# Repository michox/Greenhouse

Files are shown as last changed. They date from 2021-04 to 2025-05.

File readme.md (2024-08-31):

# Greenhouse

My mother grows her own food as a hobby and is very passionate about it. I usually benefit a lot from this hobby since as a vegetarian I get basically all my food from my mother&#39;s garden during the summer months. On top of that, organic home-grown food is not only much richer in nutrients and free of pesticides, it also tastes a lot better in my experience. Since I will be moving out and will no longer be able to help water the plants, I decided to use my engineering skills to build her an automated gardening system which takes care of her greenhouse and the three 5 m² raised bed fields.

# User Requirements

After talking to my mother about her needs with the system, I came up with the following user requirements.

| **ID** | **Description** |
| --- | --- |
| UREQ-001 | Must deliver water to 4 separate fields with an average of 20L per day on a dry, sunny day and 0-5L on a cloudy or rainy day |
| UREQ-002 | Could keep the soil at a configured moisture level between 0-100% |
| UREQ-003 | Must ventilate when the temperature in the green house reaches a user set temperature |
| UREQ-004 | Must heat actively when the temperature in the green house drops below a user set temperature |
| UREQ-005 | Should fend of snails effectively |
| UREQ-006 | Should not kill snails so as not to attract more snails |
| UREQ-007 | Must Monitor minimum and maximum temperatures over the day |
| UREQ-008 | Must be powered by solar since no grid connection is available in the garden |
| UREQ-009 | Must be low-cost |
| UREQ-010 | Must operate during 3 cloudy summer days in a row |
| UREQ-011 | Monitor must be easily readable from 50cm |
| UREQ-012 | Must be repairable |
| UREQ-013 | Must be safe |
| UREQ-014 | Must not break down in the first year |
| UREQ-015 | Should be low noise |

# System Diagram

The first thing I usually do is to define the different functional elements of a system together with inputs and outputs. I like to do that in a system diagram because it is intuitive and easy to read. I could use standardized symbols, but since I want this project to be accessible to hobbyists, I&#39;ll keep it simple and visual.

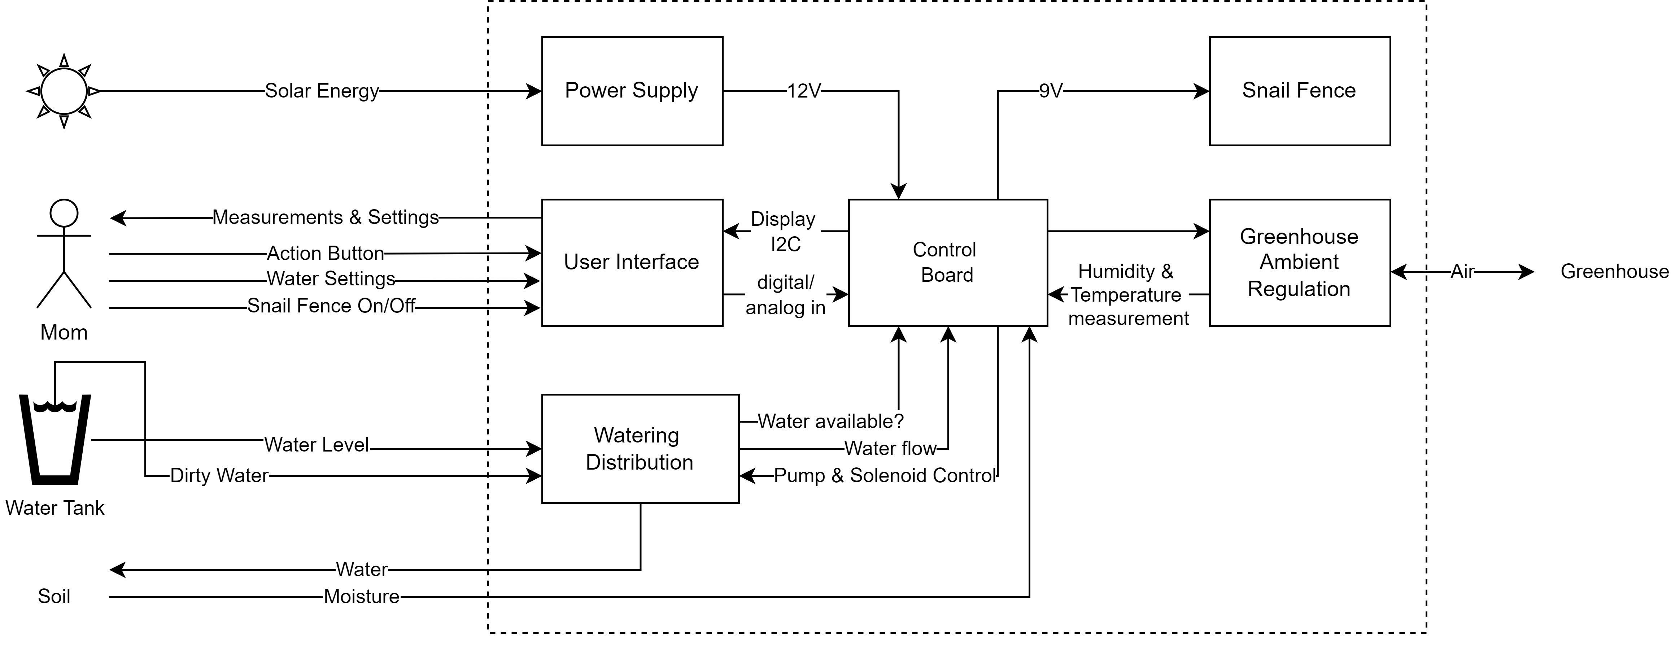
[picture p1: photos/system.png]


# System Requirements

Next, I thought about what parts my system would need to consist of and what each of these parts must fulfill to cover the user requirements. I did not take this too seriously and did not go into all the detailed module requirements like the behavior requirements of the software. This was just to document my thinking process and practice my product requirements skills a little.

| **ID** | **Description** | **Trace** |
| --- | --- | --- |
| | **Wiring** | |
| REQ-001 | All cables need to be detachable with little effort for maintenance purposes | > UREQ-011 |
| REQ-002 | All wires must exceed the standard diameters based on the rated amperage of the attached utility | > UREQ-013 |
| | **Water Distribution** | |
| REQ-011 | Must have a pump that delivers a set amount of water up to 40 Liter per day to four different locations based on user input | > UREQ-001 |
| REQ-012 | Could deliver separate amounts of water up to 40 Liter per day to four different locations based on moisture readings | > UREQ-002 |
| REQ-013 | Could have hygrometers in each field | > REQ-012 |
| REQ-014 | Must have a flowmeter with a measuring range compatible to the selected pump | > REQ-011 |
| REQ-015 | Must take the water from a water tank with potentially dirty water | > UREQ-001 |
| REQ-016 | Pump must not run dry | > UREQ-014 |
| | **User Interface** | |
| REQ-021 | Display must be at least 1.3&quot; | > UREQ-010 |
| REQ-022 | Must have a means to set the water/humidity for each field | > UREQ-001 |
| REQ-023 | Must have a means to configure the internal clock | > UREQ-001 |
| REQ-024 | Must display the minimum and maximum temperature and humidity over the day | > UREQ-007 |
| REQ-025 | Must allow to set a minimum temperature at which heating is turned on | > UREQ-004 |
| REQ-026 | Must allow to set a maximum temperature at which ventilation is turned on | > UREQ-003 |
| | **Control Board** | |
| REQ-031 | Must be protected from rain and/or condensation | > UREQ-014 |
| | **Snail Fence** | |
| REQ-041 | Must surround each of the three 1m x 5m raised beds with two copper tapes attached to a 9V power supply | > UREQ-005 > UREQ-006 |
| REQ-042 | should have a switch to turn off | > UREQ-006 |
| | **Greenhouse Ambient Regulation** | |
| REQ-051 | Must have a 12V fan | > REQ-061 > UREQ-003 |
| REQ-052 | Must have a 12V heater | > REQ-061 > UREQ-004 |
| REQ-053 | Must have a temperature and humidity sensor | > UREQ-004 |
| | **Power Supply** | |
| REQ-061 | Must have a battery with twice the capacity to power the controller module and operate the pump long enough to deliver a total of 80L per day for three days in a row. | > UREQ-001 > UREQ-008 |
| REQ-062 | Battery must be a 12V lead acid battery for cost effectiveness (because we had an old one laying around) | > UREQ-009 |
| REQ-063 | Must have a solar panel that generates enough electricity to charge the battery on an average sunny day in germany through a charge controller as constrained by> REQ-061 | > UREQ-010 > UREQ-008 |
| REQ-064 | Must provide enough power for the fan | > UREQ-003 |
| REQ-065 | Must provide enough power for the heater | > UREQ-004 |
| REQ-066 | Must provide enough power for the water distribution system | > UREQ-001 |
| REQ-067 | Must provide enough power for the snail fence | > UREQ-005 |

# System Design

Next, I started looking for parts and thinking about how I may build it cost-effectively with the parts on the market. There is no point in designing the perfect system if you can&#39;t build it because you can&#39;t find the right parts. For example, I had to get multiple adapters between thread sizes and a pressure regulator because the pump would deliver more pressure than the drip hose could endure. I made a more detailed module diagram of the water distribution since this one was the most complicated and I wanted to visualize what adaptors I needed and how everything fits together.

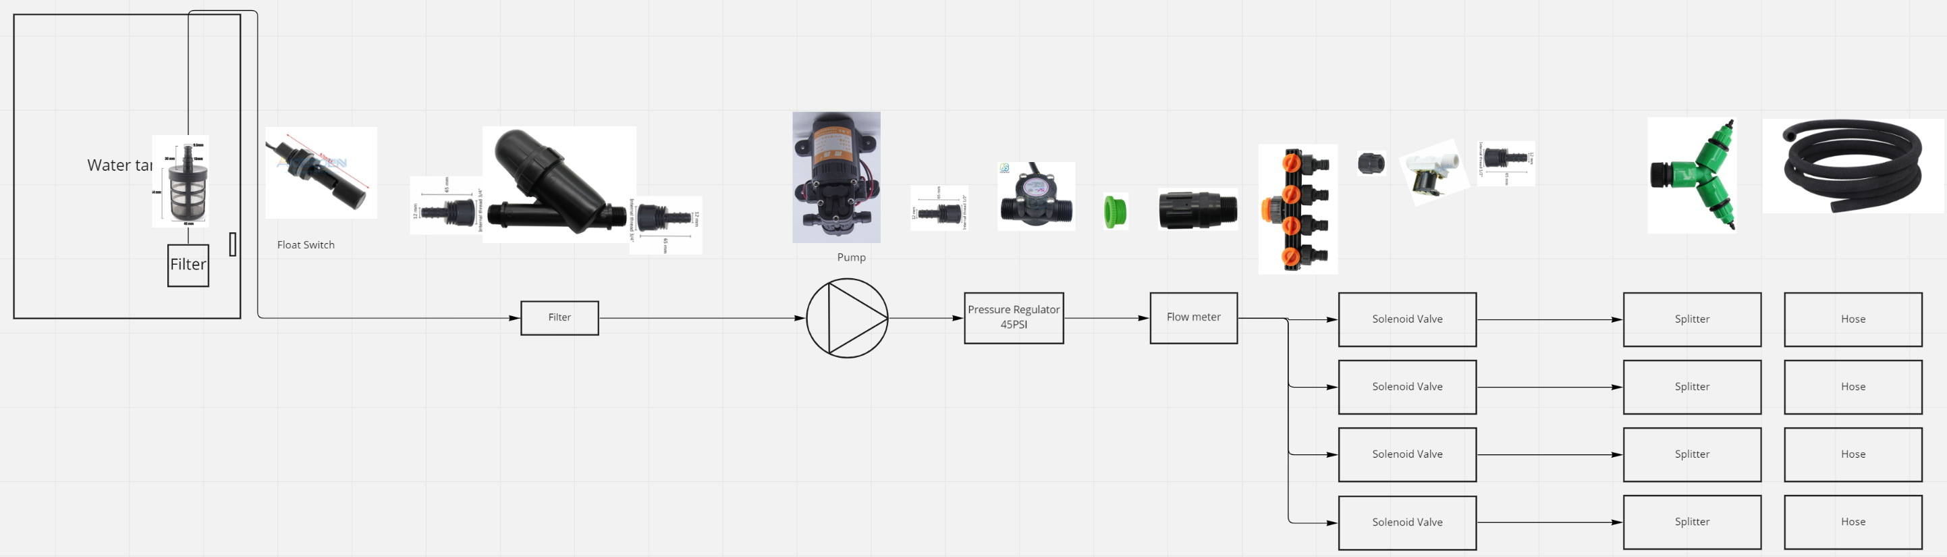
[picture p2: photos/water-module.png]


I thought about making diagrams for the electronics and software as well. but I feel like the code and electronic schematics are pretty self-explanatory, and since I am a busy man, I will leave it at that. If you have any questions, please create a github issue and I will try to answer it.

# Parts

Since my mother did not want me to spend much money, I ordered most parts from AliExpress which arrived within 2-4 weeks. Since I did not write down all requirements, traceability kind of loses its purpose so I&#39;ll leave it out.

| **ID** | **Description** | **Properties** | **Requirements** | **Quantity** | **Price €** | **Buy** |
| --- | --- | --- | --- | --- | --- | --- |
| PART-001 | Hose | 20m, 12mm inner diameter | low-cost, tolerate pressure of pump | 1 | 10 | get locally |
| PART-002 | Dripping Hose | 20m length 4/9mm, minimum of 1-2 bar working pressure, maximum of 4 bar | | 4 | 11,43 | [Link](https://www.aliexpress.com/item/32929487096.html) |
| PART-003 | Hose Clamp | 3/4&quot;, 5pc per pack | 3/4&quot; | 2 | 0,86 | [Link](https://www.aliexpress.com/item/4000954734119.html) |
| PART-004 | Pump | 5 Bar, 3.5 L/min | Flow Rate, Pressure | 1 | 8,46 | [Link](https://www.aliexpress.com/item/1005001612894964.html) |
| PART-005 | Flow Meter | 1-30L/min, 17.5 Bar, 1/2&quot; threads | 12V, can handle the pressure | 1 | 1,60 | [Link](https://www.aliexpress.com/item/4000074968315.html) |
| PART-006 | Inlet Filter | Double Net | Easy to clean, hang into water | 1 | 2,64 | [Link](https://www.aliexpress.com/item/33054351075.html) |
| PART-007 | Pre-pump Filter | 3/4&quot; threads | connectors on both ends | 1 | 6,34 | [Link](https://www.aliexpress.com/item/32906764639.html) |
| PART-008 | Pressure Regulator | 3 Bar, 3/4&quot; in female, 3/4&quot; out male, | less than 4 bar PART-002 | 1 | 1,58 | [Link](https://www.aliexpress.com/item/32917089441.html) |
| PART-009 | 1/2&quot; to 3/4&quot; adapter | | low cost UREQ-009 | 4 | 0,45 | [Link](https://www.aliexpress.com/item/4000177787641.html) |
| PART-010 | Adaptor 1/2&quot;to hose | | 1/2&quot; internal thread12mm barbed connector (PART-001) | 5 | 0,43 | [Link](https://www.aliexpress.com/item/32917141441.html) |
| PART-011 | Adaptor 3/4&quot;to hose | | 3/4&quot; internal thread12mm barbed connector (PART-001) | 2 | 0,43 | [Link](https://www.aliexpress.com/item/32917141441.html) |
| PART-012 | Fan | | 12Vlow noise | 2 | 3,27 | [Link](https://www.aliexpress.com/item/4001007637782.html) |
| PART-013 | 4 Way hose splitter | | can screw into solenoid | 1 | 5,51 | [Link](https://www.aliexpress.com/item/32923580377.html) |
| PART-014 | Soaking hose connector | | 4mm outside3/4&quot; splitter | 4 | 1,86 | [Link](https://www.aliexpress.com/item/32936271677.html) |
| PART-015 | Solenoid Valve | 1/2&quot; threads, 0.2-8 bar | runs at 12V, normally closed | 4 | 1,36 | [Link](https://www.aliexpress.com/item/33007085127.html) |
| PART-016 | Float Switch | | mounts to side of the tank | 2 | 0,64 | [Link](https://www.aliexpress.com/item/4001061701102.html) |
| PART-017 | Solar Panel | 20W | >= 4x battery capacity | 1 | 22,17 | [Link](https://www.aliexpress.com/item/32847502994.html) |
| PART-018 | Solar Charge Controller | 10A | for lead acid batteries, | 1 | 3,66 | [Link](https://www.aliexpress.com/item/33007101009.html) |
| PART-019 | Battery | 60Wh | low-cost, >= 60 Wh | 1 | 18 | get locally |
| PART-020 | Heater | | 100W, 12V | 1 | 10,59 | [Link](https://www.aliexpress.com/item/32967951841.html) |
| PART-021 | ESP32 | | low-cost, I2C interface, USB flashing, | 1 | 4,62 | [Link](https://www.aliexpress.com/item/32834130422.html) |
| PART-022 | Real Time Clock module | Based on PCF8563T | I2C, Battery mount | 1 | 0,32 | [Link](https://aliexpress.com/item/1005006438572175.html) |
| PART-023 | Hygrometer | Analog reading | 3.3V, low-cost | 8 | 0,23 | [Link](https://www.aliexpress.com/item/33048567290.html) |
| PART-024 | Bare Copper Wire | 25mx0.9mm | without enameling  | 2 | 12 | [Link](https://www.aliexpress.com/item/4000308076266.html) |
| PART-025 | 5V Step Down Converter | input 6-32V, output 5V 2A, | input 12V, output 1A | 1 | 2,18 | [Link](https://www.aliexpress.com/item/32960561943.html) |
| PART-026 | Micro USB Cable | for code uploading and powering of the USB | 20cm length, capable of data transmission | 1 | 2,18 | get locally |
| PART-027 | Button | Standard Button 12x12mm | 1 | 1 | [Link](https://www.aliexpress.com/item/32912175986.html) |
| PART-028 | I2C Display | 1.3&quot;, OLED | I2C communication | 1 | 3,15 | [Link](https://www.aliexpress.com/item/4001145494936.html) |
| PART-029 | HTU31D Humidity &amp; Temperature Sensor | 0-100% humidity, -40 to +125 C, | 0-100% humidity, -10 to +60 C, resistant to condensation, breakout so it can be lead outside of the enclosure | 1 | 2,57 | [Link](https://www.aliexpress.com/item/1005003128666097.html) |
| PART-030 | Connectors | | 2,3,4 pin connectors, suitable for selected wire diameter | 1 | 1,52 | [Link](https://www.aliexpress.com/item/32836912971.html) |
| PART-031 | Potentiometers | WTH118 linear Potentiometer | fully enclosed, else there are issues with humidity | 4 | 1,30€ | [Link](https://de.aliexpress.com/item/1005003579523720.html) | 
| PART-032 | PCB | See electronics folder for detailed BOM | | 1 | 15 | ordered from JLCPCB using the files in the electronics folder | 
| PART-033 | Barbed Connector adaptor | I 3D printed this from TPU because I realized later that I was missing this part | flexible, convert 9mm outer diameter to 12mm outer diameter | 1 | 0,05 | |

# Electronics
After a first iteration using a prototype through-hole circuit board and several bug-fixes, I upgraded to a PCB for version 2. The schematics and PCB design can be found at 
https://www.flux.ai/michox/greenhouse?editor=schematic

Since the MOQ on JLCPCB was 5 pieces I have a few more PCBs left, so if you are interested in one of those, contact me by raising an issue.

# Future Improvements
Since I regularly upload to the PCB while connected to the main power supply, I decided to use a USB step-down converter rather than an onboard voltage regulator, as I would otherwise have issues with the USB power Supply and the onboard PCB power supply. 

In the future, integrating the power supply for the ESP32 and the RTC Module would be opportunities for improvement. The PCB is also larger than necessary as I wanted to keep my old enclosure, but the PCB could easily be half the size.

I will also consider designing an enclosure for 3D printing.

# Pictures

Me assembling the box.
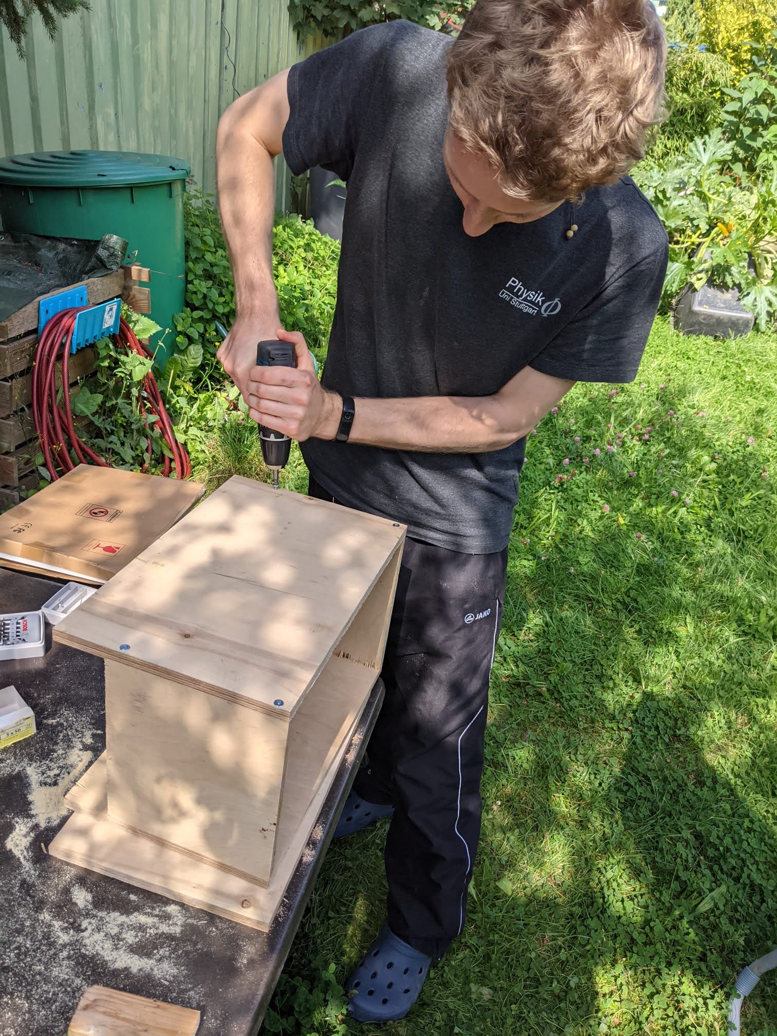
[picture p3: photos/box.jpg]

I did not have any hinges so I 3D printed some with my resin printer
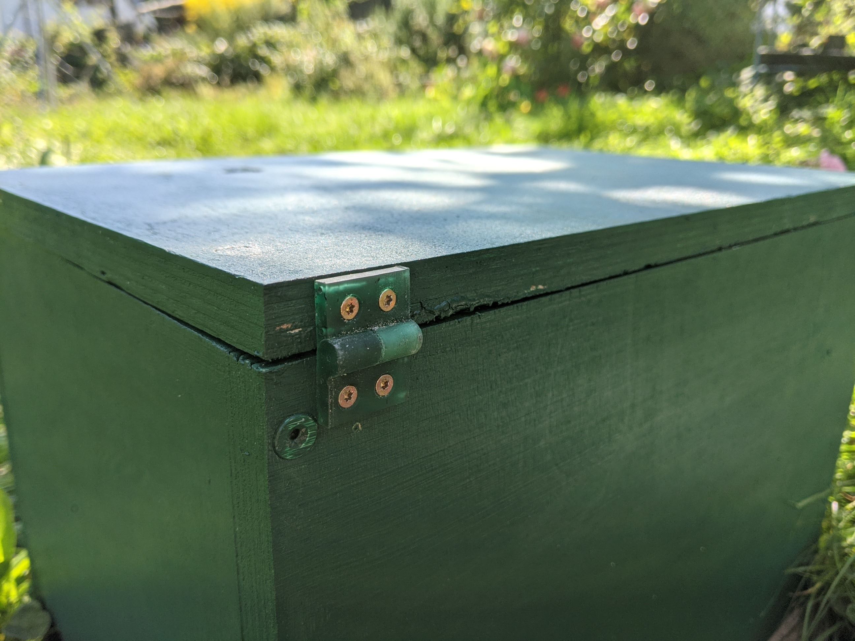
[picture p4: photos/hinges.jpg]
 
They work!
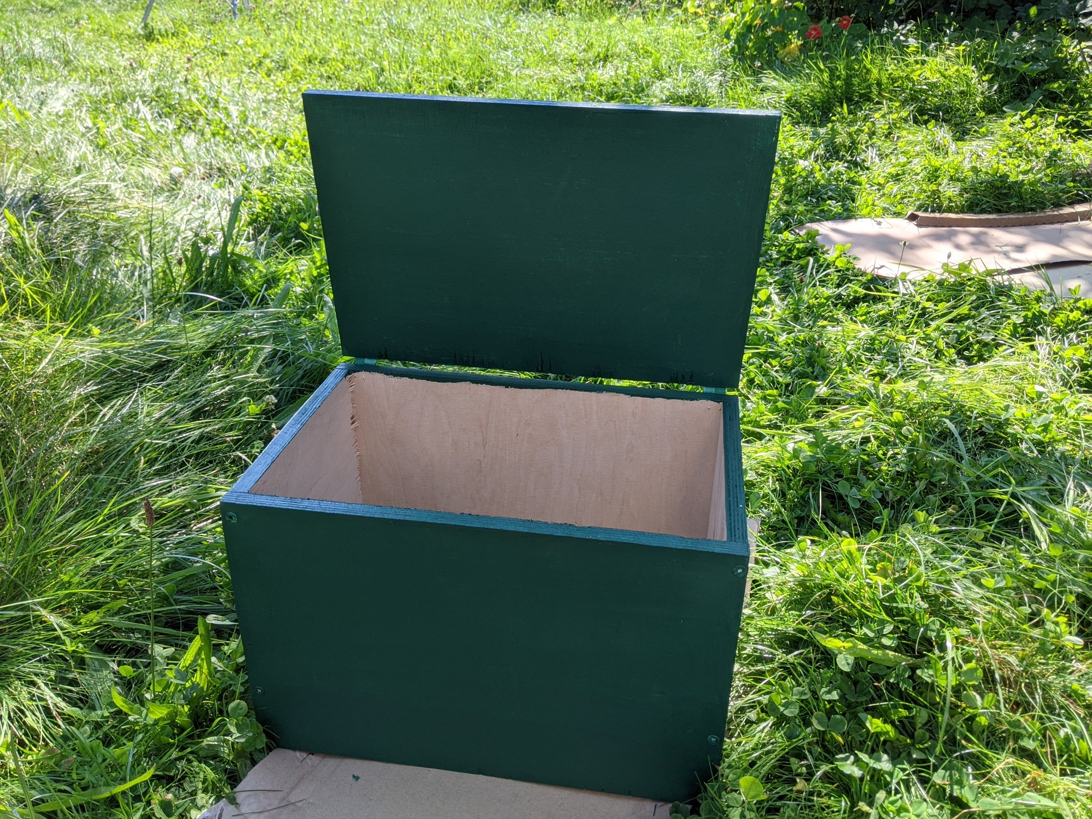
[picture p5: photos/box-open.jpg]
 
Assembling the electronics
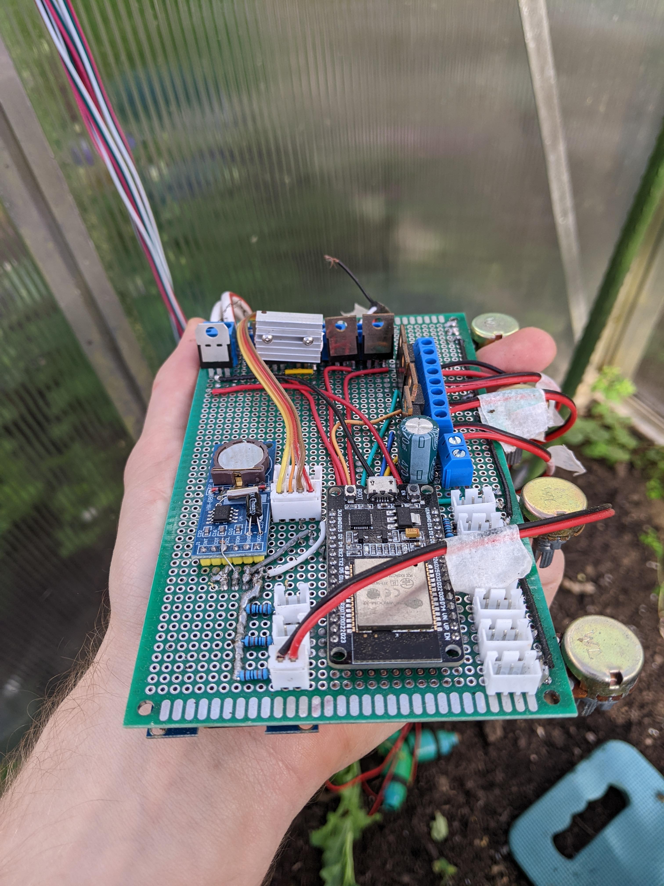
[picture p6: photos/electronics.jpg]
 
the fans
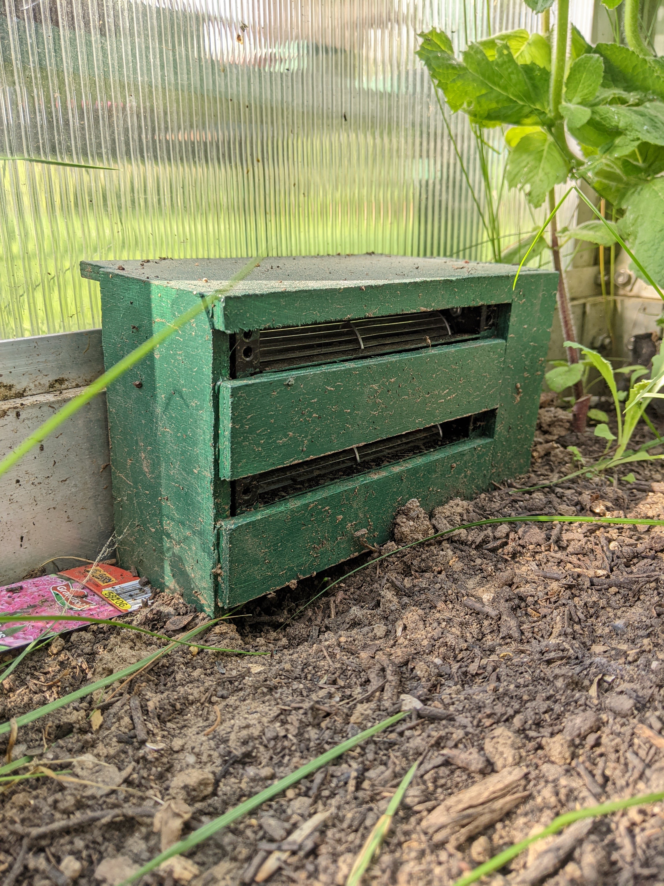
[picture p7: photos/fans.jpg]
 
this is where the fans get their air from
 
solar panel
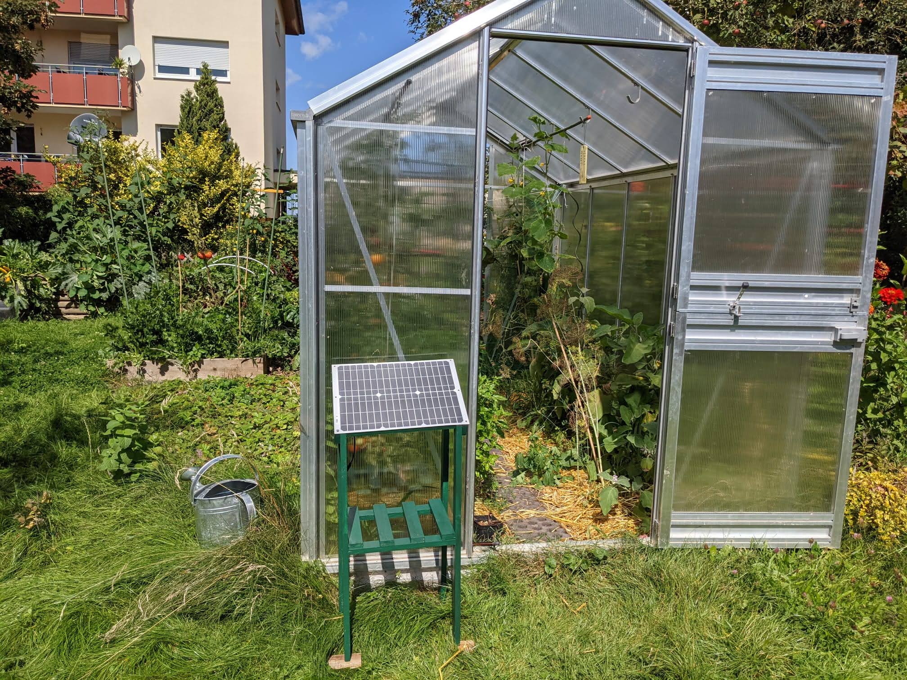
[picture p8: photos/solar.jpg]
 
battery at full charge!
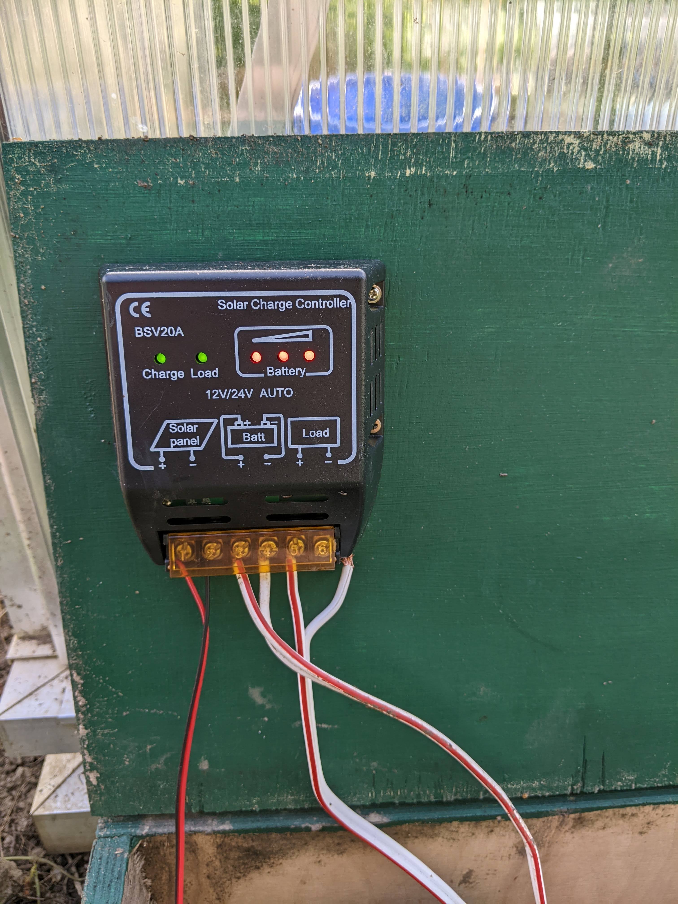
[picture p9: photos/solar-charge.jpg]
 
The snail fence
 

This is where the water is taken in
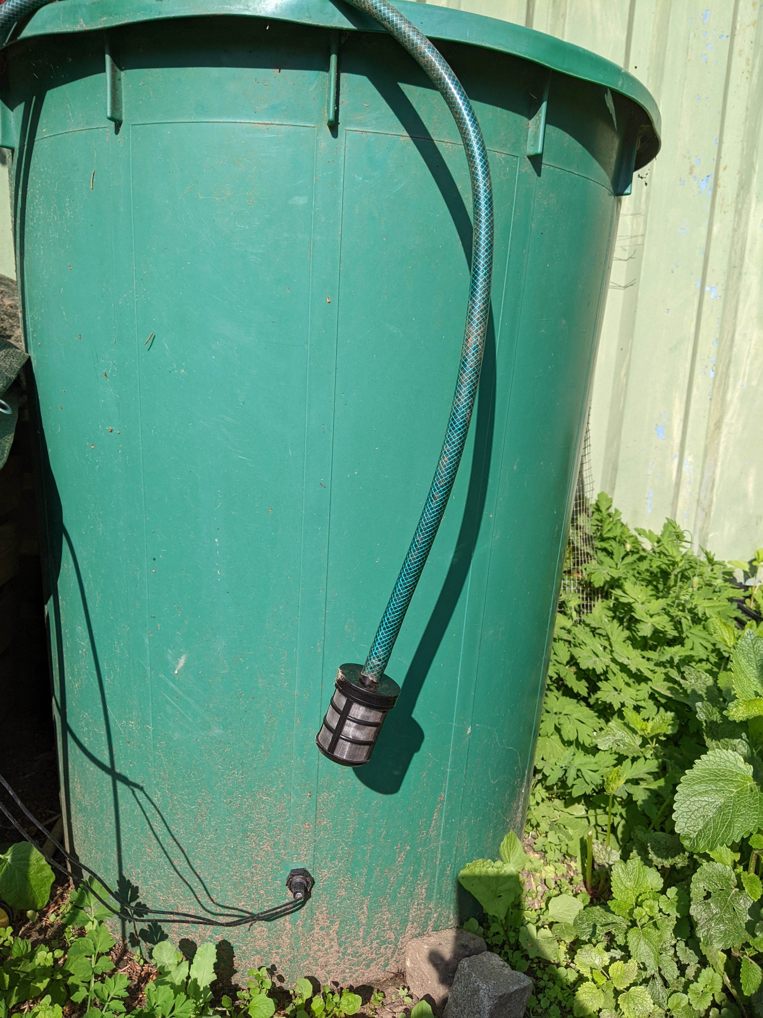
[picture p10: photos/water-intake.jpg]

Here the pump distributing it. I broke one of the connectors and need to get a replacement so it's leaking right now but that should get fixed soon.
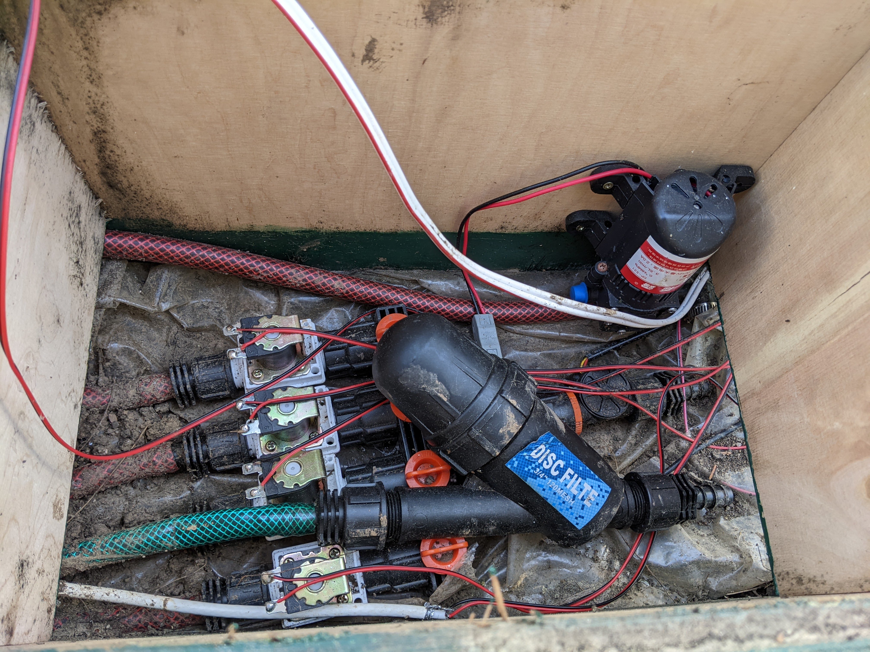
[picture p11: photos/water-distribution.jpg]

The hoses and wiring of the snail fence and hygrometers (we will install the snail fence later)
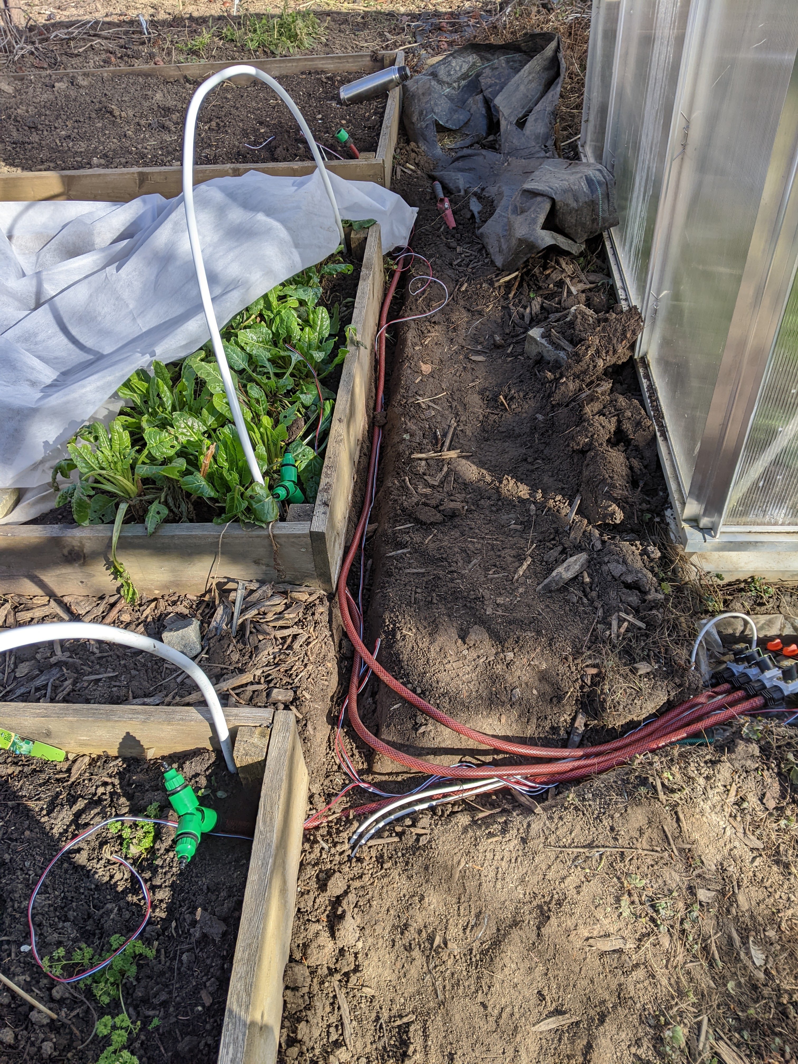
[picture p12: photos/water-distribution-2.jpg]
 
Installing the drip hoses
 
it's running!
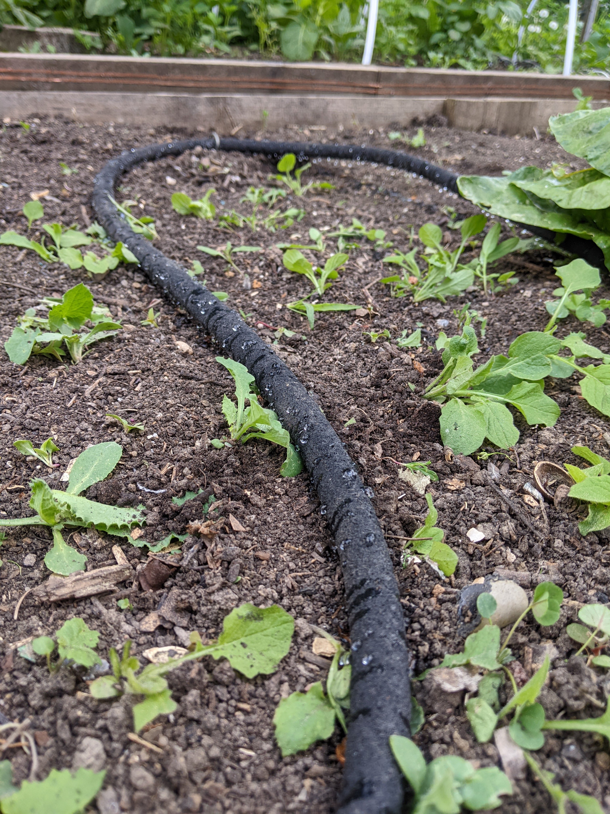
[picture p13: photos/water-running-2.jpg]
 

# Conclusion

This was a fun project and I had a chance to apply my skills in engineering and product design on a small, low risk scale which made this very enjoyable. The system is fully functional and my mom is delighted, but I will share any design improvements I come up with.

And as a final treat my mothers beautiful garden
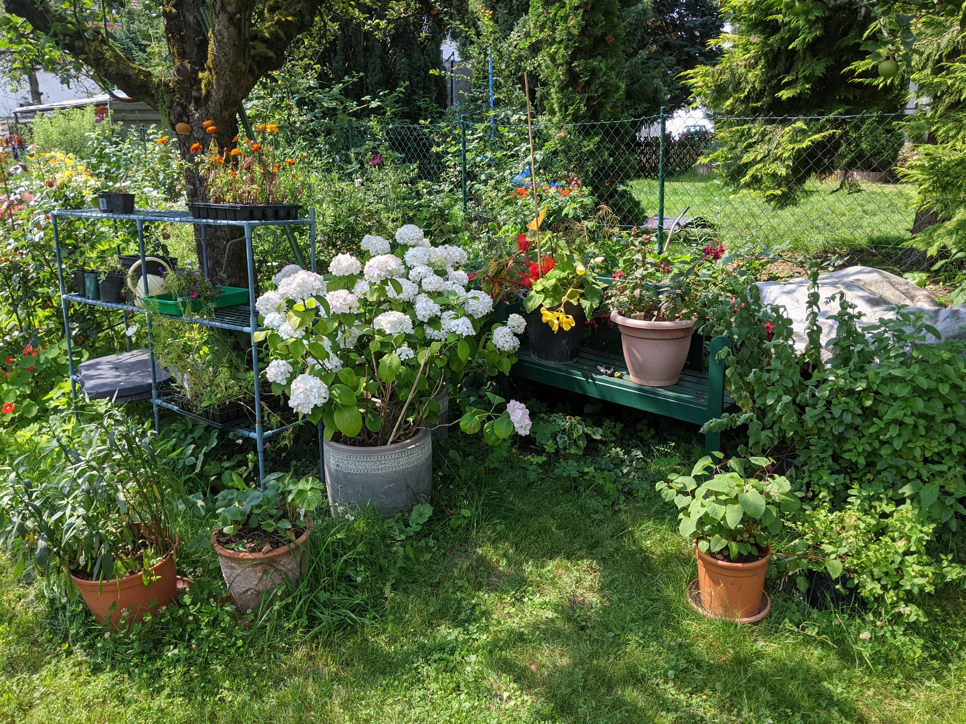
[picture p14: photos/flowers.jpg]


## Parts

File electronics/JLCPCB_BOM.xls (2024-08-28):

Comment | Designator | Footprint | JLCPCB Part #
Resistor33kΩSMD_0603_1608Metric | R19 | SMD_0603_1608Metric | C4216
Resistor3.3kΩSMD_0603_1608Metric | R21 | SMD_0603_1608Metric | C22978
AO3400A | M1_Q,M2_Q,M3_Q,M4_Q,M5_Q,M6_Q,Q2 |  | C20917
Resistor1kΩSMD_0603_1608Metric | M1_R2,M2_R2,M3_R2,M4_R2,M5_R2,M6_R2,R15,R4 | SMD_0603_1608Metric | C21190
B3B-XH-A(LF)(SN) | FLOWMETER,HYGRO1,HYGRO2,HYGRO3,HYGRO4 |  | C144394
691137710002 | BATTERY,HEATER,M1_J,M2_J,M3_J,M4_J,M5_J,M6_J,SNAIL_FENCE |  | C474881
EEE-FPV101XAV | C1 |  | C88744
Resistor100kΩSMD_0603_1608Metric | R22 | SMD_0603_1608Metric | C25803
B4B-XH-A(LF)(SN) | HTU31 |  | C144395
B2B-PH-K-S(LF)(SN) | WATERAVAILABLE |  | C158012
IRLB8721PBF | Q1 |  | C153222
Resistor10kΩSMD_0603_1608Metric | M1_R1,M2_R1,M3_R1,M4_R1,M5_R1,M6_R1,R16,R17,R18,R6 | SMD_0603_1608Metric | C22859
Resistor4.7kΩSMD_0603_1608Metric | R2,R3 | SMD_0603_1608Metric | C23162
Resistor1kΩSMD_0603_1608Metric | R20 | SMD_0603_1608Metric | C21190

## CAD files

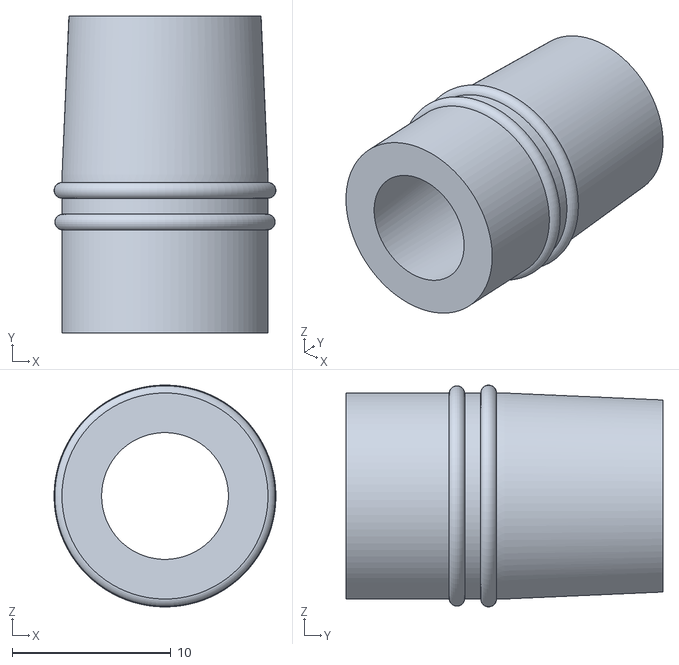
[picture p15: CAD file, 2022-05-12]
3d-prints/HoseAdaptor.stl
14.0 x 20.0 x 14.0

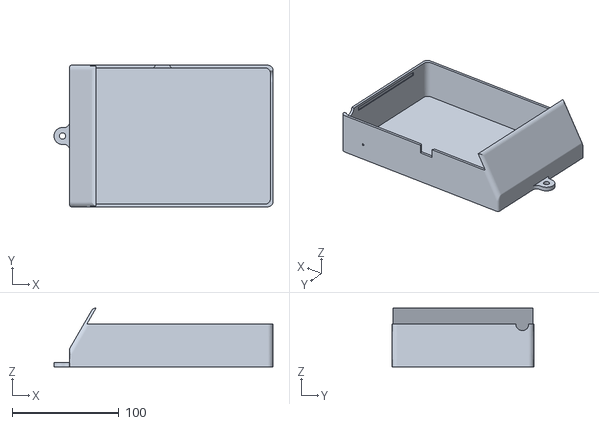
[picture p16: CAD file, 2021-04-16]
3d-prints/Case.stl
204.7 x 132.3 x 55.0

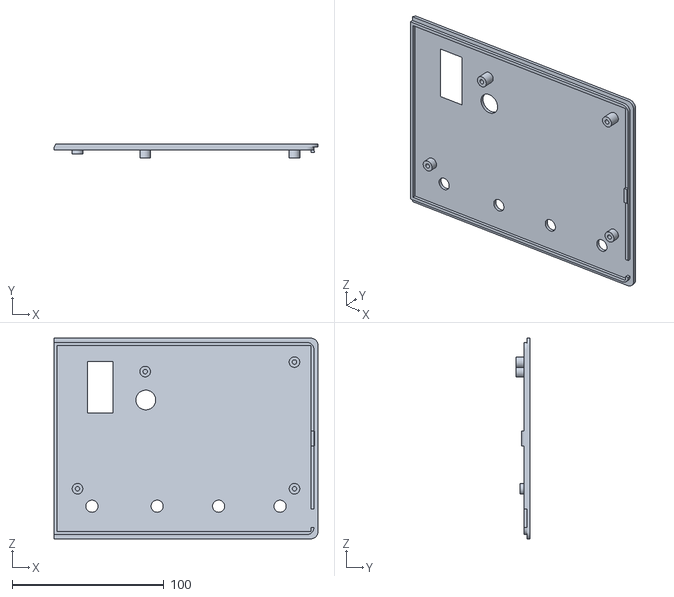
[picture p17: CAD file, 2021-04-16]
3d-prints/Fascia.stl
174.0 x 9.00 x 132.2

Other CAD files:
3d-prints/Case.ipt
3d-prints/Case_bckup.ipt
3d-prints/Fascia.ipt
3d-prints/OldVersions/Fascia.0003.ipt

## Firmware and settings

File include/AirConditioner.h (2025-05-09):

#pragma once
#include <Arduino.h>
#include "Temperature.h"
#include "Sleep.h"
#include "Preferences.h"
#include "HTU21D.h"

extern Preferences preferences;

#define DEFAULT_MIN_TEMP 5
#define DEFAULT_MAX_TEMP 27

class AirConditioner
{
private:
    int targetMaximumTemperature;
    int targetMinimumTemperature;

    bool tooCold()
    {
        if (isnan(temperature) || temperature == HTU21D_ERROR)
        {
            return false;
        }
        return (temperature < targetMinimumTemperature);
    }

    bool tooHot()
    {
        if (isnan(temperature) || temperature == HTU21D_ERROR)
        {
            return false;
        }
        return (temperature > targetMaximumTemperature);
    }

    bool warmEnough()
    {
        if (isnan(temperature) || temperature == HTU21D_ERROR)
        {
            return true;
        }
        return (temperature > targetMinimumTemperature + 2);
    }

    bool coolEnough()
    {
        if (isnan(temperature) || temperature == HTU21D_ERROR)
        {
            return true;
        }
        return (temperature < targetMaximumTemperature - 2);
    }

public:
    AirConditioner()
    {
    }

    void begin()
    {
        pinMode(HEATER, OUTPUT);
        pinMode(FAN, OUTPUT);
        digitalWrite(HEATER, RELAY_OFF);
        digitalWrite(FAN, RELAY_OFF);
        this->targetMaximumTemperature = preferences.getInt("maxTemp", DEFAULT_MAX_TEMP);
        this->targetMinimumTemperature = preferences.getInt("minTemp", DEFAULT_MIN_TEMP);
    }

    void setMaximumTemperature(int temp)
    {
        targetMaximumTemperature = temp;
        preferences.putInt("maxTemp", temp);
    }

    void setMinimumTemperature(int temp)
    {
        targetMinimumTemperature = temp;
        preferences.putInt("minTemp", temp);
    }

    int getMaximumTemperature() { return targetMaximumTemperature; }
    int getMinimumTemperature() { return targetMinimumTemperature; }

    void regulate()
    {
        if (tooCold())
        {
            working++;
            Serial.printf("working++ heater. working : %d\n", working);

            while (!warmEnough())
            {
                Serial.println("heating");
                gpio_hold_dis(HEATER);
                digitalWrite(HEATER, RELAY_ON);
                gpio_hold_en(HEATER);
                vTaskDelay(3000 / portTICK_PERIOD_MS);
            }
            gpio_hold_dis(HEATER);
            digitalWrite(HEATER, RELAY_OFF);
            gpio_hold_en(HEATER);
            working--;
            Serial.printf("working-- heater. working : %d\n", working);
        }
        else if (tooHot())
        {
            working++;
            Serial.printf("working++ fan. working : %d\n", working);

            while (!coolEnough())
            {
                Serial.println("Cooling...");
                gpio_hold_dis(FAN);
                digitalWrite(FAN, RELAY_ON);
                gpio_hold_en(FAN);
                vTaskDelay(3000 / portTICK_PERIOD_MS);
            }
            gpio_hold_dis(FAN);
            digitalWrite(FAN, RELAY_OFF);
            gpio_hold_en(FAN);
            working--;
            Serial.printf("working-- fan. working : %d\n", working);
        }
    }
};

extern AirConditioner ac;

void airConditioningTask(void *);

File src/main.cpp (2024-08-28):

#include <Arduino.h>
#include <FreeRTOS.h>
#include "ButtonTask.h"
#include "AirConditioner.h"
#include "SnailFence.h"
#include "Watering.h"
#include "Display.h"
#include "Sleep.h"
#include "Clock.h"
#include "Pinout.h"

Preferences preferences;
SemaphoreHandle_t mutex = NULL;
SemaphoreHandle_t wateringMutex = NULL;


void setup()
{
  esp_sleep_pd_config(ESP_PD_DOMAIN_RTC_SLOW_MEM, ESP_PD_OPTION_ON);
  snailFenceController.init();
  Serial.begin(115200);
  preferences.begin("Greenhouse");
  mutex = xSemaphoreCreateMutex();
  wateringMutex = xSemaphoreCreateMutex();
  xTaskCreate(temperatureMeasuringTask, "measure temp", configMINIMAL_STACK_SIZE + 5000, NULL, 10, NULL);
  xTaskCreate(flowMeasuringTask, "measure flow", configMINIMAL_STACK_SIZE + 5000, NULL, 10, NULL);
  xTaskCreate(floatSwitchTask, "float switch", configMINIMAL_STACK_SIZE + 1000, NULL, 1000, NULL);
  xTaskCreate(buttonTask, "button", configMINIMAL_STACK_SIZE + 5000, NULL, 10, NULL);
  xTaskCreate(wateringTask, "watering", configMINIMAL_STACK_SIZE + 5000, NULL, 11, NULL);
  xTaskCreate(airConditioningTask, "ac", configMINIMAL_STACK_SIZE + 5000, NULL, 10, NULL);
  xTaskCreate(displayTask, "display", configMINIMAL_STACK_SIZE + 5000, NULL, 20, NULL);
  xTaskCreate(clockTask, "clock", configMINIMAL_STACK_SIZE + 5000, NULL, 20, NULL);
  Wire.setClock(10000);
  Serial.printf("Setup complete\n");
}

void loop()
{
  vTaskDelay(500/portTICK_PERIOD_MS);
  if (!working)
  {
    goToSleep();
  }
}

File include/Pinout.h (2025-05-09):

#pragma once
#include <FreeRTOS.h>

#define RELAY_ON HIGH
#define RELAY_OFF LOW

#define HYGRO_1 GPIO_NUM_36
#define HYGRO_2 GPIO_NUM_39
#define HYGRO_3 GPIO_NUM_34
#define HYGRO_4 GPIO_NUM_35
#define AREA_POTI_1 GPIO_NUM_32
#define AREA_POTI_2 GPIO_NUM_33
#define AREA_POTI_3 GPIO_NUM_25
#define AREA_POTI_4 GPIO_NUM_26
#define AREA_SOLENOID_1 GPIO_NUM_5 

#define AREA_SOLENOID_2 GPIO_NUM_17
#define AREA_SOLENOID_3 GPIO_NUM_16
#define AREA_SOLENOID_4 GPIO_NUM_4

#define FLOW_METER GPIO_NUM_27

#define WATER_AVAILABLE GPIO_NUM_23

#define PUMP GPIO_NUM_12
#define HEATER GPIO_NUM_21
#define FAN GPIO_NUM_12

#define SNAIL_MONITOR GPIO_NUM_18
#define SNAIL_FENCE GPIO_NUM_19

#define BUTTON GPIO_NUM_2

extern SemaphoreHandle_t mutex;
extern SemaphoreHandle_t wateringMutex;

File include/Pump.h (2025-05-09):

#pragma once
#include "Arduino.h"
#include "Pinout.h"
#include "FlowMeter.h"

extern RTC_DATA_ATTR boolean pumpIsBlocked;

class Pump
{
public:
    int32_t ticksSincePumpStart = -1;   
    void begin()
    {
        pinMode(PUMP, OUTPUT);
        stop();
    }
    void run()
    {
        if (!isRunning())
        {
            ticksSincePumpStart = 0;
        }
        gpio_hold_dis(PUMP); //to enable hold during deep sleep and keep the pins pulled low.
        digitalWrite(PUMP, RELAY_ON);
        gpio_hold_en(PUMP);
    }
    void stop()
    {
        ticksSincePumpStart = -1;
        gpio_hold_dis(PUMP);
        digitalWrite(PUMP, RELAY_OFF);
        gpio_hold_en(PUMP);
    }
    bool isRunning()
    {
        return digitalRead(PUMP) == RELAY_ON;
    }

    bool notBlocked()
    {
        if (pumpIsBlocked) return false;
        if (ticksSincePumpStart < 100)
        {
            pumpIsBlocked = false;
        }
        else if (averageFlow > 0.1)
        {
            Serial.println("Pump is running, flow: " + String(averageFlow) + " l/h");
            pumpIsBlocked = false;
        }
        else
        {
            #ifdef DEBUG
            pumpIsBlocked = false;
            #else
            pumpIsBlocked = true;
            #endif
        }
        return !pumpIsBlocked;
    }
};
extern Pump pump;

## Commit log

2021-04-16 replaced DHT22 with HTU21D
    [AirConditioner.h, Temperature.cpp]
2021-07-21 updated electrical schematic and added water low frame
    [Electronics.sch]
2021-07-21 updated electronics
    [Electronics.kicad_pcb, Electronics.sch]
2021-07-21 annotations and added regulator to electronics
    [Electronics.sch]
2022-05-12 added photos and readme, updated electronics
    [Case top.0004.ipt, Case.0006.ipt, Case.stl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]
2023-05-02 general changes and stability fixes
    [AirConditioner.h, Display.cpp]
2024-08-26 version 2
    [Electronics.kicad_pcb, Electronics.sch, JLCPCB_BOM.xls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]
2024-08-31 updated libraries and readme
    [Case top.ipt, Case.ipt, Case_bckup.ipt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]
2025-05-09 bug fixes and stability improvements
    [AirConditioner.h, Display.cpp, Pinout.h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]
